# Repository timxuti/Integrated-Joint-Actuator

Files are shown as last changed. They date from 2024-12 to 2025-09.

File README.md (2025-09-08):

# 3D-Printed Integrated Joint Actuator 



## V5 (Current): Complete Redesign (07/22/25 - Current)
This is a complete redesign of everything. This iteration features a reduction of 23:1, removed the ring post bearings for dowel pins, added a pair of 6710-2RS bearings for output shaft support, improved file structures, etcetcetc. TLDR this version should be actually not trash.


### Fixes:
- Cycloidal disk fracturing
- Redesigned the gearbox assembly completely, removing print quality issues with the outer wall
- Fixed rotor clearance issues
- Fixed rotor centering
- Added moment support for output
- No more heat-set insert for load-bearing parts, changed to M4 hex nut
- Added proper ODrive S1 Mounting
- Added bearings for output from inside cycloidal disks
### Issues:
- Hard to print with FDM (lots of support and post-processing needed)
- Plastic can only take you so far ): cycloidal disk still fractures under load, considering changing to aluminum or acetal
- ODrive S1 sticks out way too much, wanted to use ODrive Micro but out of stock ):
- Pins grind through cycloidal disk fast
- Wire still sticks out of motor and not encased  
<br />

## Subcomponents and File Naming
Custom parts should obey the XXXX YZZ - NAME file number convention:  
- XXX: Module ID (Alphabetical)  
- Y: File type classifier (Numbers)  
- ZZ: Part number (Numbers)  
- NAME: Descriptive file name in Title Capitalization Form  

### Module IDs  
- BLDC: Brushless DC Motor  
- CYC: Internal Cycloidal Gearbox  
- COTS: Commercial Off the Shelf  
- ODS1: ODrive S1 Mounting  

### File Classifiers
- 0: Top-level assemblies (No more than 1)  
- 1: Subassemblies  
- 2: Equation.txt files  
- 3: Drawings  
- 4: Individual parts  
- 5: Wiring, piping, tubing, and weldments   
- 6: Test fit files  
- 7: Misc. files (Textures, Scenarios, Simulations)   
- 8: Solidworks VISUALIZE files  
- 9: Manufacturing files (3MF, STL, DXF, GCODE)

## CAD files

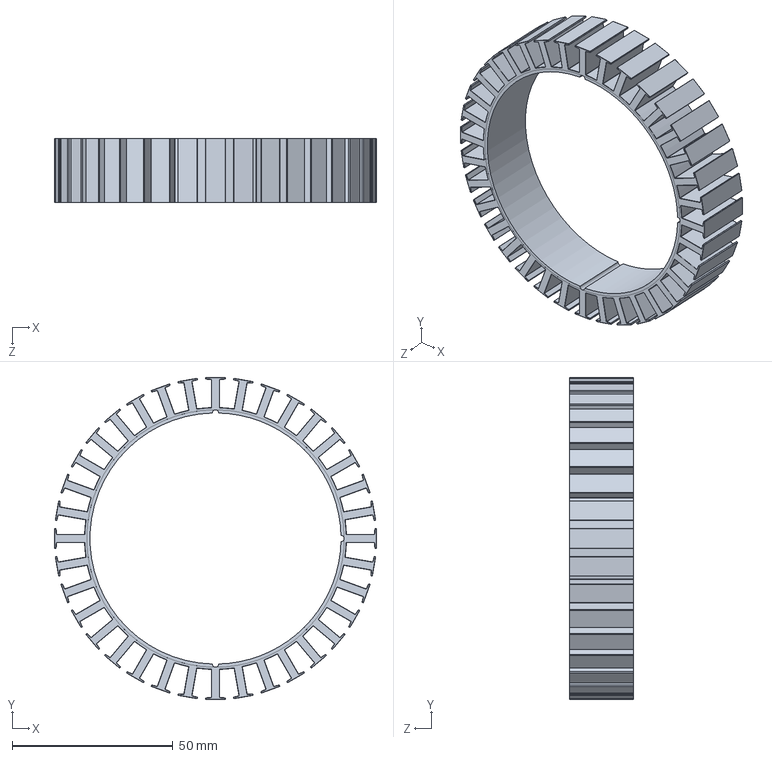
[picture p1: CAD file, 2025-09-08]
CAD/BLDC/BLDC 401 - 100mm Outrunner Stator.SLDPRT
100.0 x 100.0 x 20.0 mm

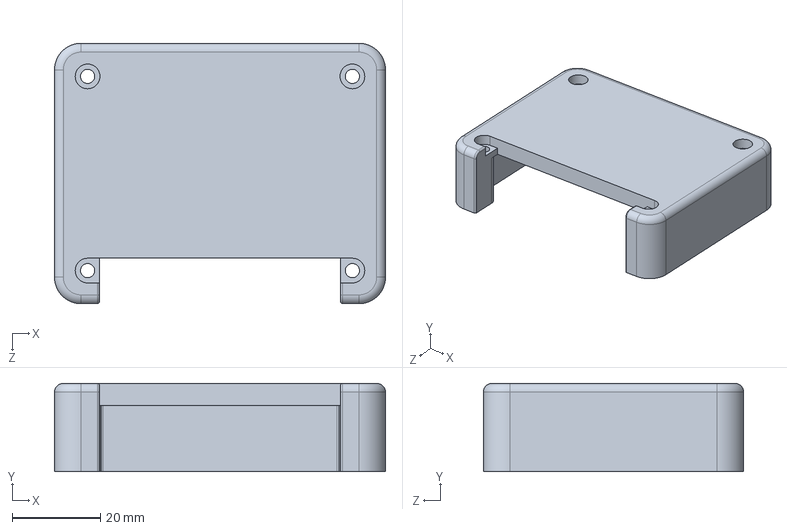
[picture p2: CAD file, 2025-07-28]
CAD/ODS1/ODS1 402 - ODrive S1 Cover.SLDPRT
75.0 x 20.0 x 59.0 mm

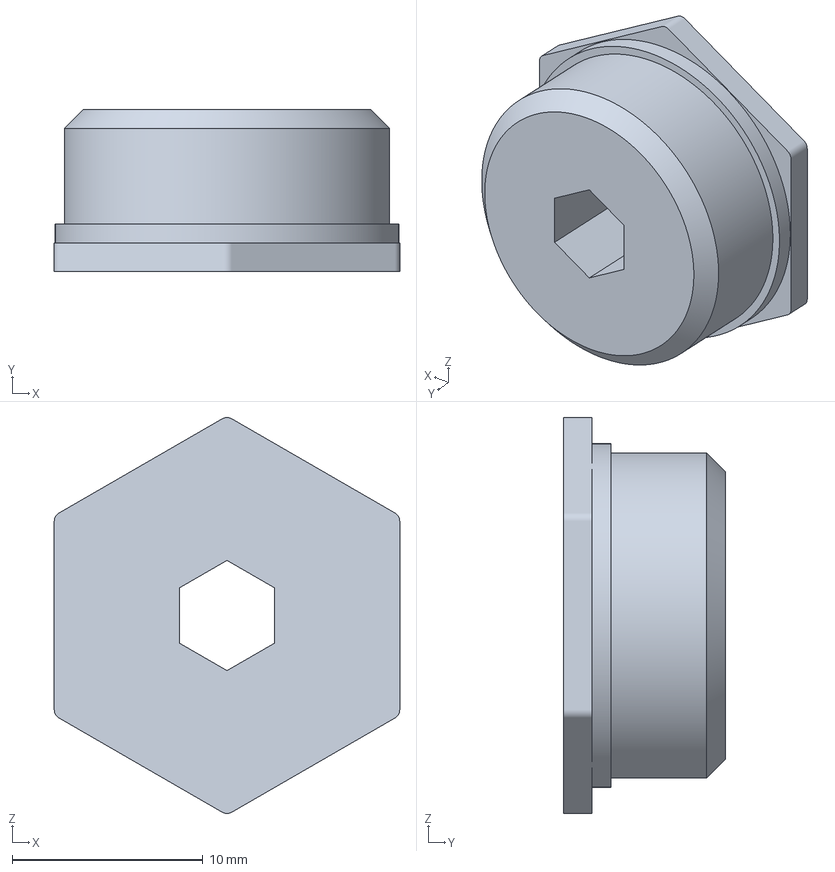
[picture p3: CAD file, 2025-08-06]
CAD/Print Export V2/BLDC 404.1 - THRU Rotor Bearing Adapter.3MF
18.1 x 8.50 x 20.7 mm

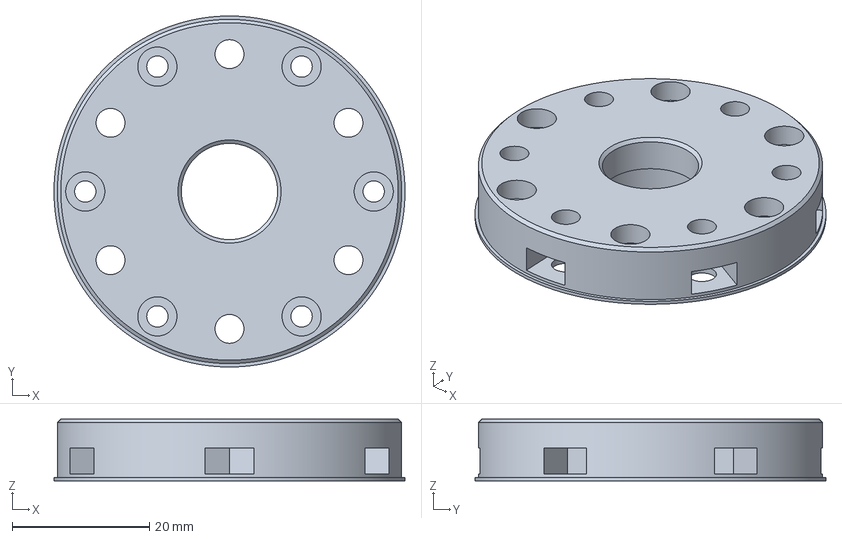
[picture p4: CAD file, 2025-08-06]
CAD/Print Export V2/Print 2/CYC 406 - Output Front Interface.3MF
51.1 x 51.1 x 9.00 mm

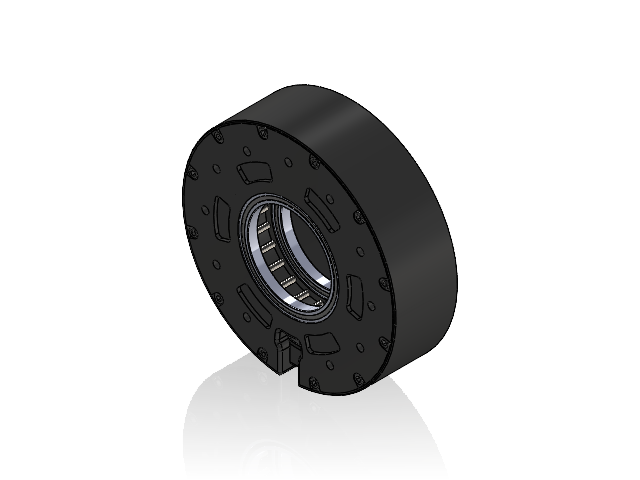
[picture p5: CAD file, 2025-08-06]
CAD/CYC/CYC 104 - Cycloidal Housing Assembly.SLDASM
CYC 401 - Cycloidal Housing
CYC 408 - Actuator Top Cover
CYC 410 - Actuator Housing
3x20 Dowel Pin x 24
50x62x6 Radial Bearing 6710-2RS x 2
17x23x4 Radial Bearing 6703-2RS
Ruthex Insert M3x5.7 x 24
M3x20 Socket Head x 12
M4 Hex Nut x 11
M3x15 Socket Head x 12

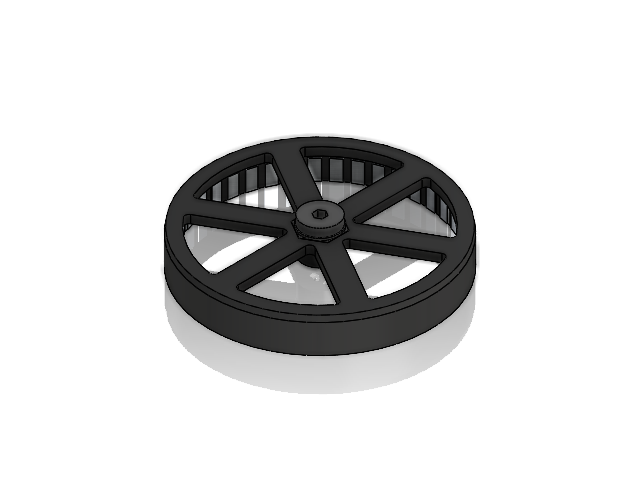
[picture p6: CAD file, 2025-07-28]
CAD/Print Export V2/Reference Subassemblies/BLDC 102 - Rotor Assembly.SLDASM
BLDC 403 - Rotor Body
BLDC 404 - Rotor Bearing Adapter

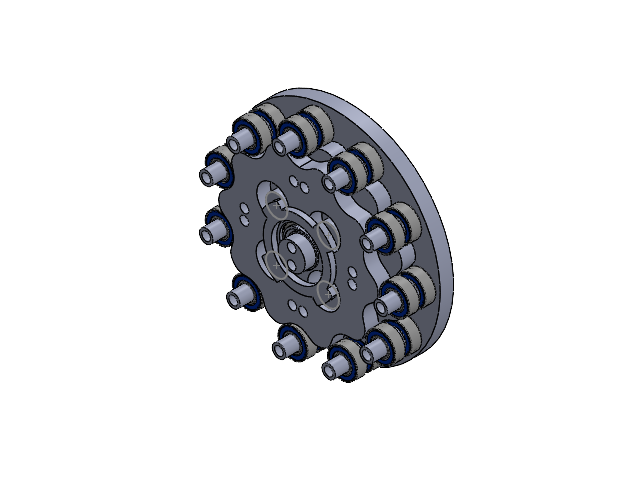
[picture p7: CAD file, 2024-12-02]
CAD/QDD V0/CYC/CYC 101 - Cycloidal Gearbox REV1.SLDASM
25x32x4 Ball Bearing 4648K325
5x11x4 Ball Bearing 4668K225 x 22
10x15x4 Shielded Ball Bearing 6656K163 x 2
CYC 401 - Gearbox Bottom
CYC 402 - Cycloidal Disk x 2
CYC 403 - Ring Post x 11
CYC 404 - Ring Spacer x 11
CYC 405 - Center Shaft
CYC 406 - Ring Spacer 2mm x 11
CYC 407 - Center Shaft Spacer x 2
CYC 408 - Gearbox Output REV2

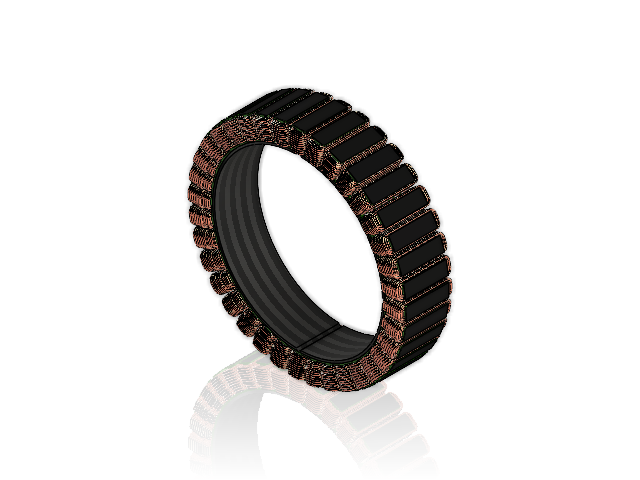
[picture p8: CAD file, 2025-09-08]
CAD/BLDC/BLDC 101 - 10020 Motor Stator Assembly.SLDASM
BLDC 401 - 100mm Outrunner Stator
BLDC 402 - 19AWG Stator Motor Winding x 36

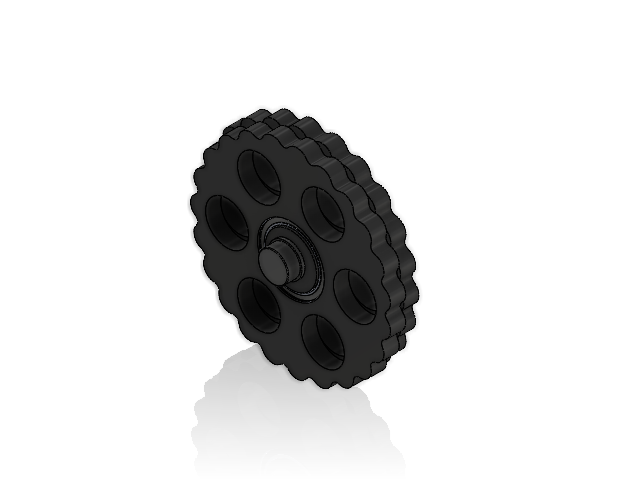
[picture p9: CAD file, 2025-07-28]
CAD/Print Export V2/Reference Subassemblies/CYC 103 - Input Shaft Assembly.SLDASM
CYC 402 - Offset Cam x 2
CYC 403 - 1mm Input Shaft Spacer x 2
CYC 404 - Cycloidal Disk x 2
CYC 407 - Input Shaft Cap

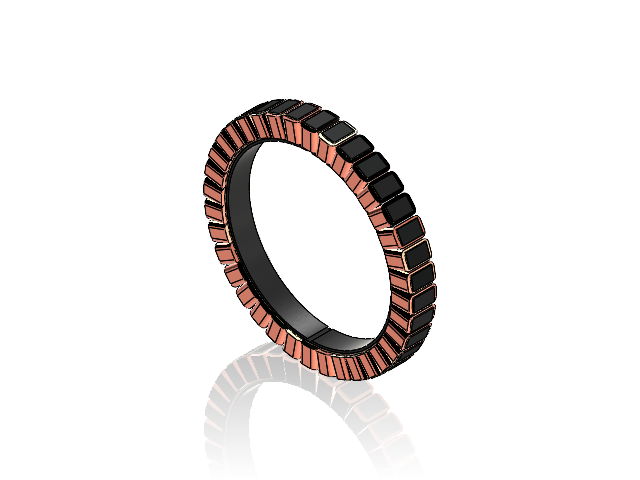
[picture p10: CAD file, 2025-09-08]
CAD/BLDC/BLDC 101 - Stator Assembly.SLDASM
BLDC 401 - Motor Stator
BLDC 402 - Stator Coil x 36

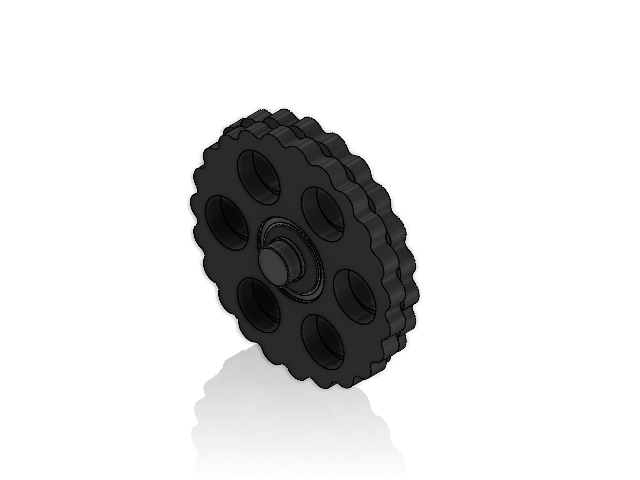
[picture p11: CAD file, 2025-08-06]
CAD/CYC/CYC 103 - Input Shaft Assembly.SLDASM
CYC 402 - Offset Cam x 2
M2 Hexnut x 2
DIN913 M2.0 L6 x 2
CYC 403 - 1mm Input Shaft Spacer x 2
CYC 404 - Cycloidal Disk x 2
5m Hex
17x23x4 Radial Bearing 6703-2RS x 2
CYC 407 - Input Shaft Cap

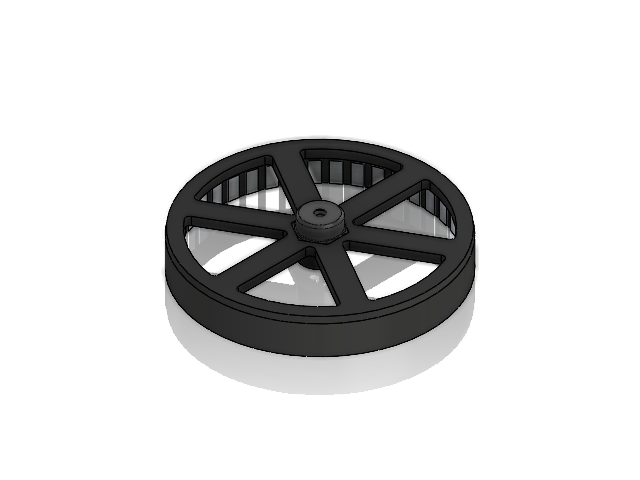
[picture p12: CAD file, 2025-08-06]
CAD/BLDC/BLDC 102 - Rotor Assembly.SLDASM
BLDC 403 - Rotor Body
BLDC 404 - Rotor Bearing Adapter
M2 Hex Nut x 2
DIN913 M2.0 L4 x 2
Magnet 10x5x2 x 42

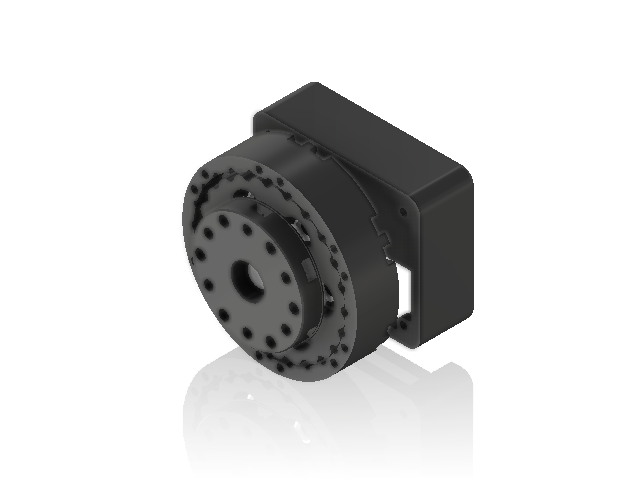
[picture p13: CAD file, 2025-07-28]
CAD/Print Export V2/IJA 001 - Print Export - Integrated Joint Actuator Assembly.SLDASM
CYC 405 - Output Back Bearing Interface
CYC 406 - Output Front Interface
CYC 409 - 1.5mm Spacer D6 x 12
CYC 409.1 - 2mm Spacer D6 x 6
CYC 402 - Offset Cam x 2
CYC 403 - 1mm Input Shaft Spacer x 2
CYC 404 - Cycloidal Disk x 2
CYC 407 - Input Shaft Cap
CYC 401 - Cycloidal Housing
BLDC 404 - Rotor Bearing Adapter
ODS1 401 - ODrive S1 Spacer
ODS1 402 - ODrive S1 Cover

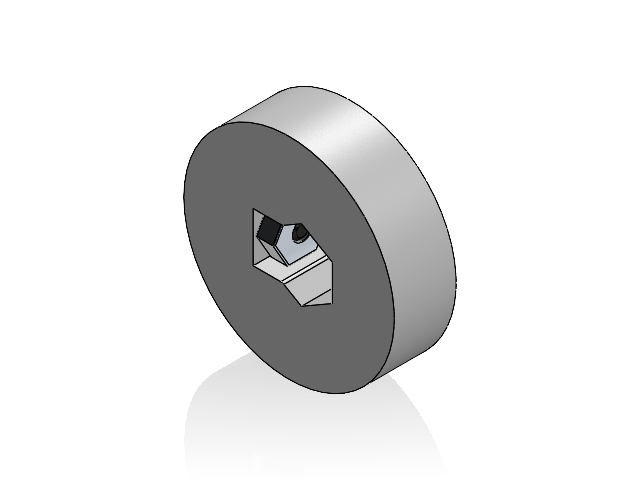
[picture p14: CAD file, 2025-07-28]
CAD/CYC/CYC 102 - Offset Cam Assembly.SLDASM
CYC 402 - Offset Cam
M2 Hexnut
DIN913 M2.0 L6

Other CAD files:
CAD/Print Export V2/Reference Subassemblies/CYC 102 - Offset Cam Assembly.SLDASM
CAD/CYC/CYC 101 - Cycloidal Output Assembly.SLDASM
CAD/Print Export V2/Reference Subassemblies/CYC 104 - Cycloidal Housing Assembly.SLDASM
CAD/CYC/CYC 001 - Cycloidal Gearbox Assembly.SLDASM
CAD/BLDC/BLDC 402 - 19AWG Stator Motor Winding.SLDPRT
CAD/BLDC/BLDC 402 - Stator Coil.SLDPRT
CAD/BLDC/BLDC 403 - Rotor Body.SLDPRT
CAD/BLDC/BLDC 404 - Rotor Bearing Adapter.SLDPRT
CAD/BLDC/BLDC 404.1 - THRU Rotor Bearing Adapter.SLDPRT
CAD/COTS/10x15x4 Radial Bearing 6700-2RS.SLDPRT
CAD/COTS/10x15x4 Shielded Ball Bearing 6656K163.SLDPRT
CAD/COTS/17x23x4 Radial Bearing 6703-2RS.SLDPRT
CAD/COTS/17x26x5 Radial Bearing 6803-2RS.SLDPRT
CAD/COTS/3x20 Dowel Pin.SLDPRT
CAD/COTS/45x55x6 Radial Bearing 6709-2RS.SLDPRT
CAD/COTS/50x62x6 Radial Bearing 6710-2RS.SLDPRT
CAD/COTS/5m Hex.SLDPRT
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

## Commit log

2024-12-01 QDD Init
    [QDD V1.SLDASM]
2024-12-01 Motor Stator
    [BLDC 401 - Motor Stator.SLDPRT]
2024-12-01 Stator Assembly
    [BLDC 101 - Stator Assembly.SLDASM, BLDC 401 - Motor Stator.SLDPRT, BLDC 402 - Stator Coil.SLDPRT]
2024-12-02 CYC Half
    [CYC 101 - Cycloidal Gearbox REV1.SLDASM, CYC 401 - Gearbox Bottom.SLDPRT, CYC 402 - Cycloidal Disk.SLDPRT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]
2024-12-02 save v2
    [CYC 101 - Cycloidal Gearbox REV1.SLDASM, CYC 408 - Gearbox Output REV2.SLDPRT, CYC 408 - Gearbox Output.SLDPRT]
2024-12-02 CYC Feature Complete
    [30x37x4 Ball Bearing 4648K326.SLDPRT, CYC 403 - Ring Post.SLDPRT, CYC 408 - Cycloidal Output.SLDPRT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]
2024-12-02 Gearbox Complete
    [CYC 403 - Ring Post.SLDPRT, CYC 405 - Center Shaft.SLDPRT, CYC 405.1 - Center Shaft Bottom.SLDPRT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]
2024-12-03 QDD V0
    Oh my god im finally done thank the fucking lords now i have to study for finals plz end me now
    [BLDC 101 - Stator Assembly.SLDASM, BLDC 102 - Rotor Assembly.SLDASM, BLDC 403 - Rotor Body.SLDPRT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]
2024-12-04 Top Plate REV 4
    [CYC 410 - Gearbox Top.SLDPRT, CYC 903 - Gearbox Top REV4.3MF]
2024-12-05 QDD V1
    [10x15x4 Shielded Ball Bearing 6656K163.SLDPRT, 25x32x4 Ball Bearing 4648K325.SLDPRT, 30x37x4 Ball Bearing 4648K326.SLDPRT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]
2024-12-12 QDD V1 + V2 Init
    [10x15x4 Shielded Ball Bearing 6656K163.SLDPRT, 25x32x4 Ball Bearing 4648K325.SLDPRT, 30x37x4 Ball Bearing 4648K326.SLDPRT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]
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2024-12-14 V3 Initiated
    [CYC 301 - Cycloidal Disk REV2.dxf, CYC 401 - Gearbox Bottom.SLDPRT, CYC 402 - Cycloidal Disk REV2.SLDPRT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]
2025-01-08 CYC Backplate Update
    [BLDC 102 - Rotor Assembly.SLDASM, BLDC 404 - Rotor Shaft.SLDPRT, CYC 401 - Gearbox Bottom.SLDPRT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]
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2025-01-11 Housing V3 Complete
    [BLDC 102 - Rotor Assembly.SLDASM, BLDC 404 - Rotor Shaft.SLDPRT, CYC 301 - Cycloidal Disk REV3.dxf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]
2025-01-11 QDD V3 Complete
    [40x50x6 Shielded Ball Bearing 4668K261.SLDPRT, CYC 301 - Cycloidal Disk REV3.dxf, CYC 402 - Cycloidal Disk REV3.SLDPRT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]
2025-01-12 Fixed mates
    [CYC 408 - Cycloidal Output.SLDPRT]
2025-01-17 V3 Complete
    [CYC 408 - Cycloidal Output.SLDPRT]
2025-01-18 V3 Print
    [BLDC 102 - Rotor Assembly.SLDASM, BLDC 403 - Rotor Body.SLDPRT, BLDC 404 - Rotor Shaft.SLDPRT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]
2025-01-18 QDD V3
    [QDD 603 - QDD 3D Print.SLDASM, QDD 903 - QDD Back Housing.STL]
2025-01-19 Stand Adapter
    [BLDC 102 - Rotor Assembly.SLDASM, BLDC 404 - Rotor Shaft.SLDPRT, CYC 401 - Gearbox Bottom.SLDPRT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]
2025-01-19 Create STAND 902 - Stand Adapter.3mf
    [STAND 902 - Stand Adapter.3mf]
2025-01-19 QDD Test Stand
    [QDD 602 - TEST PRINT QDD Fit Check.SLDASM, QDD 904 - QDD Stand.STL, TST 401- QDD Stand.SLDPRT]
2025-01-20 Fixed QDD Stand Insert Diam.
    [QDD 904 - QDD Stand.STL, TST 401- QDD Stand.SLDPRT]
2025-01-21 Test Stand w/ Odrive S1
    [BLDC 102 - Rotor Assembly.SLDASM, BLDC 404 - TEST Rotor Shaft.SLDPRT, CYC 101 - Cycloidal Gearbox REV1.SLDASM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]
2025-01-22 Cycloidal Output V2
    [CYC 101 - Cycloidal Gearbox REV1.SLDASM, CYC 408 - Cycloidal Output.SLDPRT, QDD 602 - TEST PRINT QDD Fit Check.SLDASM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]
2025-02-02 QDD Rev4 Init
    [10x15x4 Shielded Ball Bearing 6656K163.SLDPRT, 25x32x4 Ball Bearing 4648K325.SLDPRT, 30x37x4 Ball Bearing 4648K326.SLDPRT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]
2025-02-05 QDD V4 Progress
    [BLDC 102 - Rotor Assembly.SLDASM, BLDC 404 - TEST Rotor Shaft.SLDPRT, CYC 101 - Cycloidal Gearbox REV1.SLDASM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]
2025-03-22 KSED Update
    [10x15x4 Shielded Ball Bearing 6656K163.SLDPRT, 40x50x6 Shielded Ball Bearing 4668K261.SLDPRT, BLDC 101 - Stator Assembly.SLDASM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]
2025-07-22 Init QDD V5
    [10x15x4 Shielded Ball Bearing 6656K163.SLDPRT, 25x32x4 Ball Bearing 4648K325.SLDPRT, 30x37x4 Ball Bearing 4648K326.SLDPRT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]
2025-07-23 Wiped files to start work on V5
    [BLDC 102 - Rotor Assembly.SLDASM, BLDC 403 - Rotor Body.SLDPRT, BLDC 404 - Rotor Shaft.SLDPRT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]
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2025-07-24 Added input shaft assembly and changed rotor assembly interface
    Changed the input shaft assembly to be a 5mm hex and added the Cams and Cycloidal disks. Changed the rotor assembly to accept the 5mm hex.
    [17x23x4 Radial Bearing 6703-2RS.SLDPRT, 50x62x6 Radial Bearing 6710-2RS.SLDPRT, 5m Hex.SLDPRT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]
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2025-07-25 Completed CAD with COTS hardware
    [10x15x4 Radial Bearing 6700-2RS.SLDPRT, BLDC 101 - Stator Assembly.SLDASM, BLDC 102 - Rotor Assembly.SLDASM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]
2025-07-25 Added front face pocketing and cable cutouts
    [CYC 104 - Cycloidal Housing Assembly.SLDASM, CYC 408 - Actuator Top Cover.SLDPRT, IJA 401 - Actuator Housing.SLDPRT]
2025-07-26 Completely finished with ODrive S1 modeled
    [CYC 103 - Input Shaft Assembly.SLDASM, CYC 104 - Cycloidal Housing Assembly.SLDASM, CYC 404 - Cycloidal DiskV1.SLDPRT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]
2025-07-26 Init Visualize Project, Added lighting
    [CYC 103 - Input Shaft Assembly.SLDASM, CYC 404 - Cycloidal Disk.SLDPRT, CYC 404 - Cycloidal DiskV1.SLDPRT]
2025-07-28 Prototyping print files and dimension changes
    Lots and lots of test print files, because I accidently turned on the "Auto circle contour hole compensation" feature, and it screwed up all the tolerances for the entire assembly ): wasted a good 600+g of filament bc of that. Lesson learned.
    [BLDC 101 - Stator Assembly.SLDASM, BLDC 102 - Rotor Assembly.SLDASM, BLDC 401 - Motor Stator.SLDPRT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]
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2025-08-06 V5 Prototype with test stand
    [BLDC 102 - Rotor Assembly.SLDASM, BLDC 404 - Rotor Bearing Adapter.3MF, BLDC 404 - Rotor Bearing Adapter.SLDPRT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]
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2025-09-08 IJA V6 w/ 10020 stator
    [BLDC 101 - 10020 Motor Stator Assembly.SLDASM, BLDC 101 - Stator Assembly.SLDASM, BLDC 401 - 100mm Outrunner Stator.SLDPRT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]
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
